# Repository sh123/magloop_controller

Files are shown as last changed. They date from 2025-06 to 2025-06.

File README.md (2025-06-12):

# Magnetic loop antenna capacitor controller
Magnetic loop antenna capacitor controller based on 
 - OpenSCAD project to generate custom sliding variable high voltage capacitors with two predefined configurations
 - Arduino Nano
 - L298N stepper driver
 - EM-290 stepper from Epson printer
 - HC-06 bluetooth serial controller for remote control using Bluetooth console application from the phone or PC
 - Generated high voltage 3d printed slide capacitor printed with PETG plastic (up to ~15kV and 130pF)
   - Plate sizes are ~70x55 mm
   - Capacitor dimensions are 60x70x80 mm
   - Plate spacing 5 mm
   - 14 plates
   - Worm gear is M4
   - Can handle 100W CW without arcing (tested with 0.9m loop) and continous 50W operation in FT8
   - Capacitance range ~5-130 pF
   - Can tune ~9-29 MHz with 0.9m loop
 - Second test generated medium voltage 3d printed slide capacitor up to ~6 kV and higher 400pF capacitance

# Serial commands
On successful command execution "ok" is returned when operation was successfully completed or "err" if command was unsuccessful. Next commands are supported:
 - Movements
   - *p*: park to initial 0 position, automatically performed when powered on
   - *u*, *uu*, *uuu*: go/tune up to higher frequency (5/50/500kHz steps)
   - *d*, *dd*, *ddd*: go/tune down to lower frequency (5/50/500kHz steps)
   - *freqkhz*, frequency in kHz where to move capacitor, should be used after calibration procedure completion
 - Calibration
   - *t*: print calibration table
   - *c[freqkhz]*: store current minimum swr position into given calibration frequency cell
   - *s*: save calibration table

# Configuration parameters (capctrl.h)
 - *ConfigSpeed*: stepper speed, default is 64
 - *ConfigStep(5|50|500)kHz*: number of steps for tune up/down commands for 5/50/500kHz steps
 - *ConfigMaxPos*: end position of capacitor, maximum number of steps, default is 5200
 - *ConfigCalPoints*: number of calibration points, default is 23
 - *ConfigCalAddr*: EEPROM start address where calibration data is stored, default is 0x0
 - *ConfigStepCompensate*: number of steps for reverse compensation when changing direction

# Photos

- Large capacitor 15kV/130pF

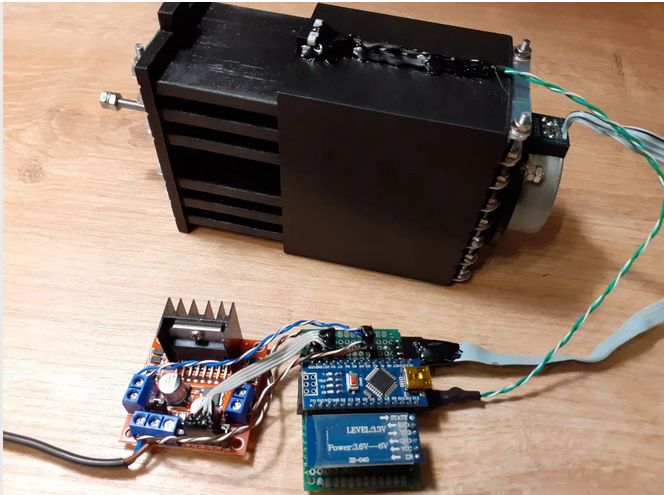
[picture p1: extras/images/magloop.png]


-  Medium size capacitor with lower maximum voltage, but larger capacitance 6kV/400pF

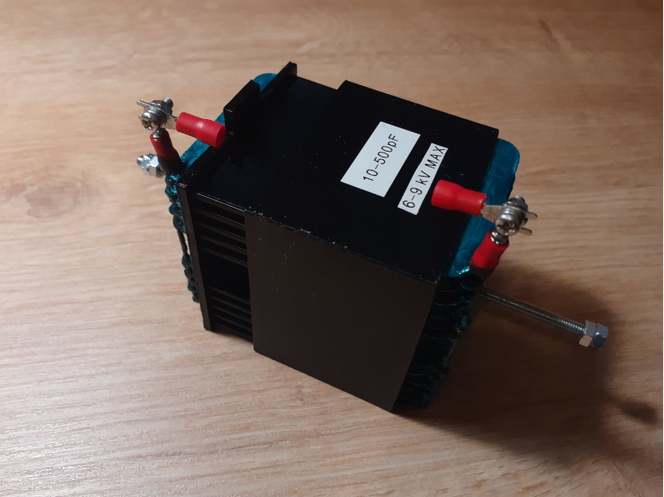
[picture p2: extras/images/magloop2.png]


- Test magnetic loop antenna, 1m loop diameter, 40mm tube diameter, fed using inductive coupling from smaller loop and 1:1 balun

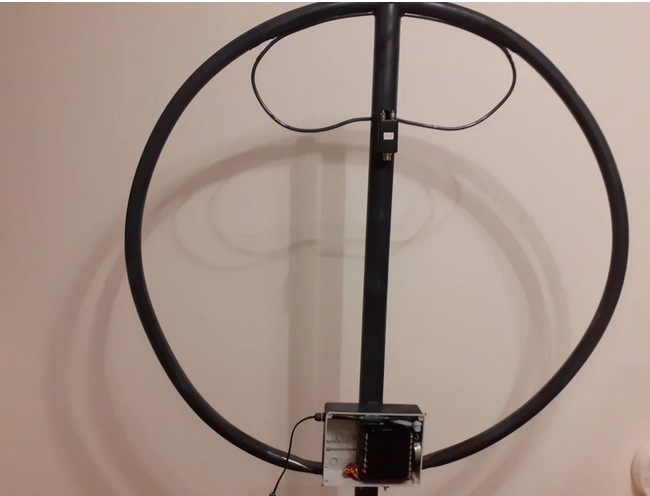
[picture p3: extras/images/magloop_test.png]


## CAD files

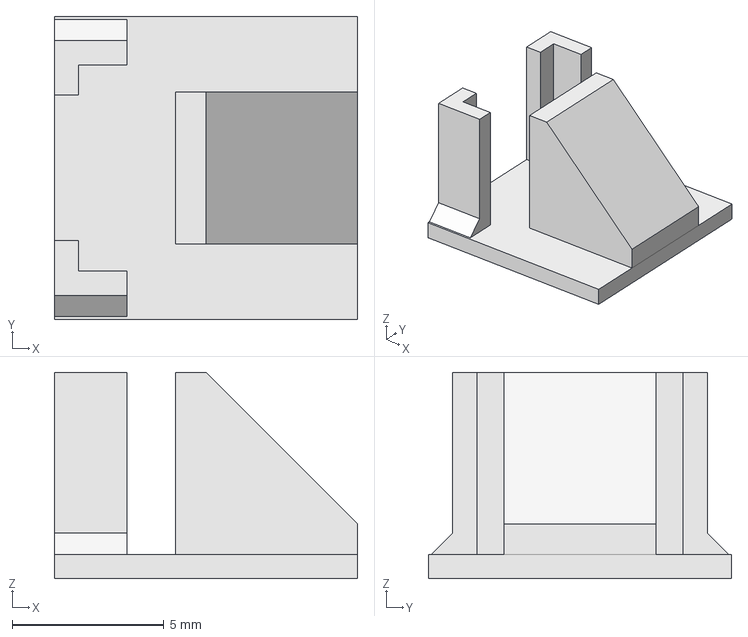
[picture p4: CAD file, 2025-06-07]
extras/cad/btn_holder.FCStd
10.0 x 10.0 x 6.80 mm

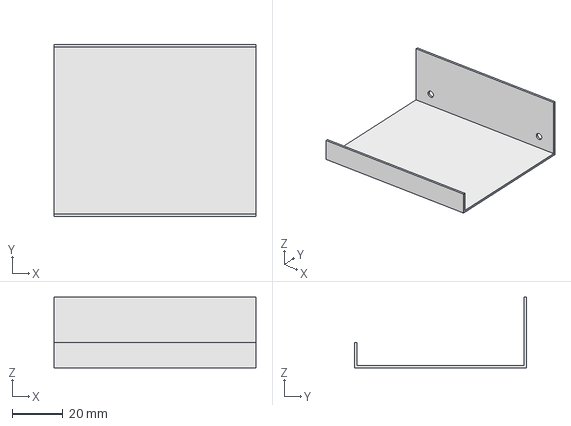
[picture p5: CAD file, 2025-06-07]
extras/cad/electronics_holder.FCStd
80.0 x 68.0 x 28.0 mm

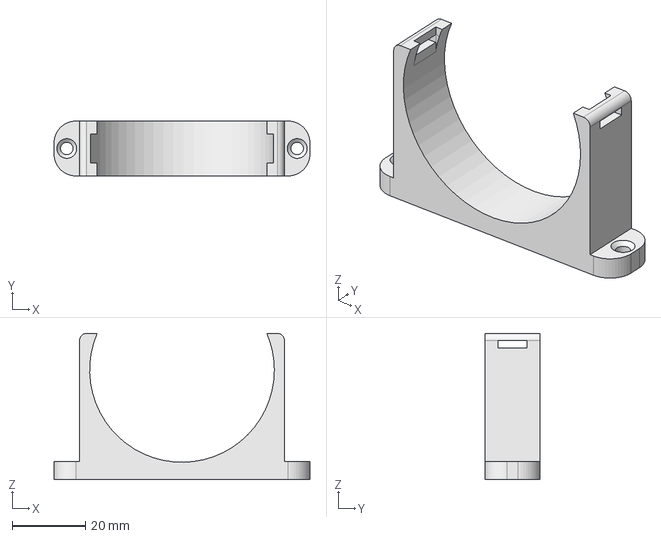
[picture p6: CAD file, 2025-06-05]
extras/cad/box_holder.FCStd
70.0 x 15.0 x 40.0 mm

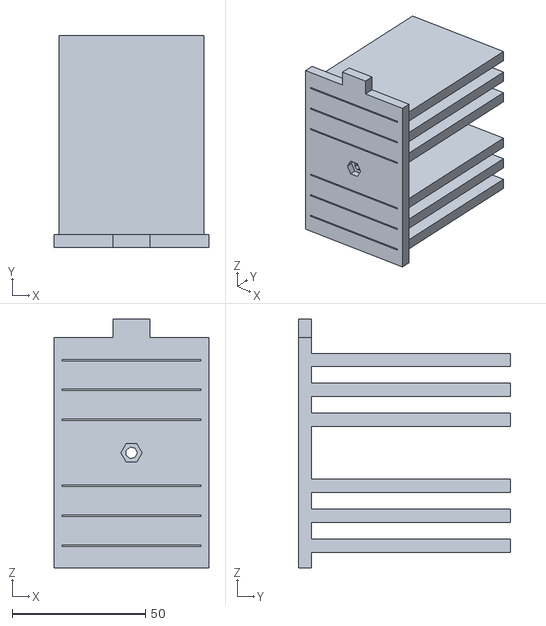
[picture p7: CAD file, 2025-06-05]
extras/cad/15kv_130pf_rotor.stl
58.0 x 79.7 x 93.4

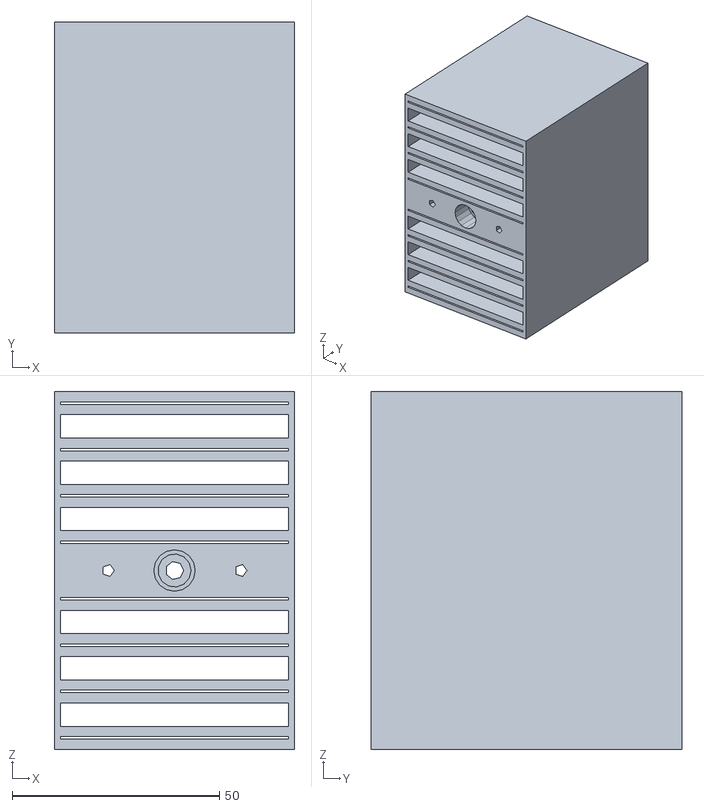
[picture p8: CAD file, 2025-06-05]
extras/cad/15kv_130pf_stator.stl
58.0 x 75.0 x 86.4

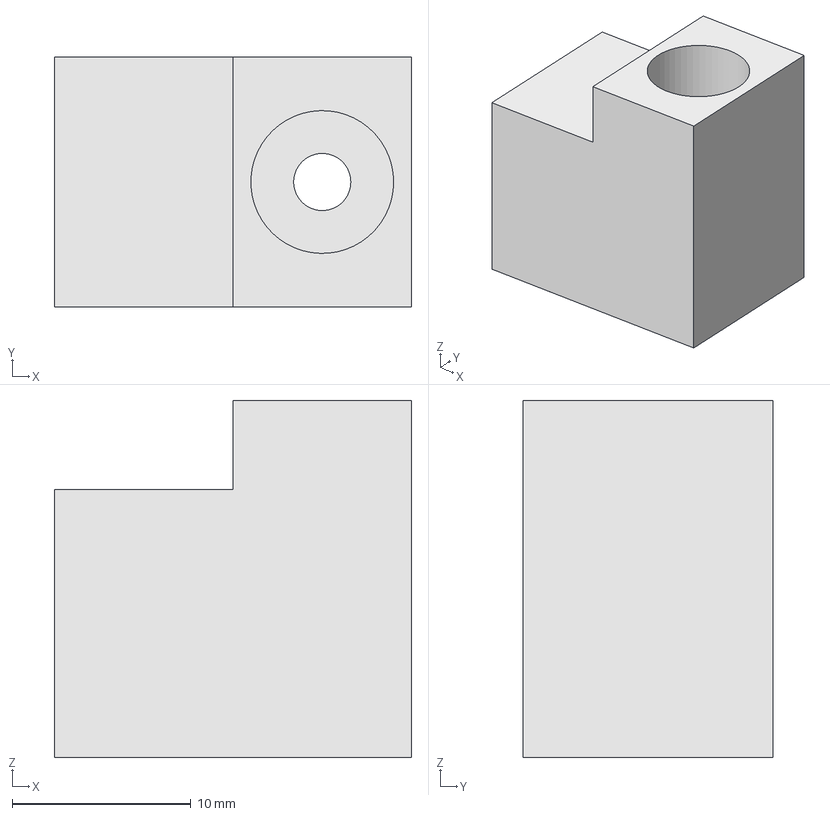
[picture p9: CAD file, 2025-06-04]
extras/cad/cap_stands_15mm.FCStd
20.0 x 14.0 x 20.0 mm

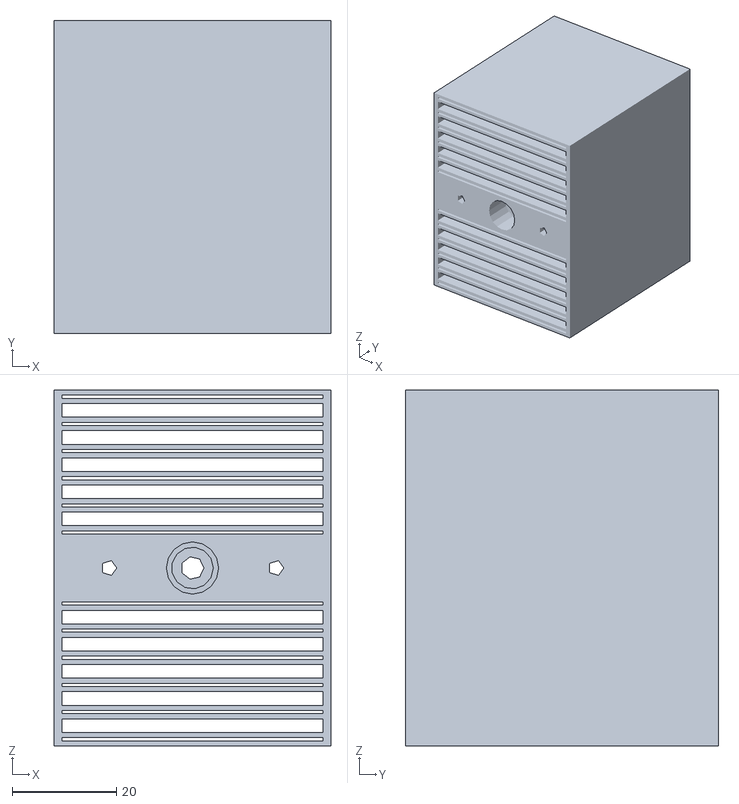
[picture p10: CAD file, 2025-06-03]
extras/cad/6kv_400pf_stator.stl
53.0 x 60.0 x 68.2

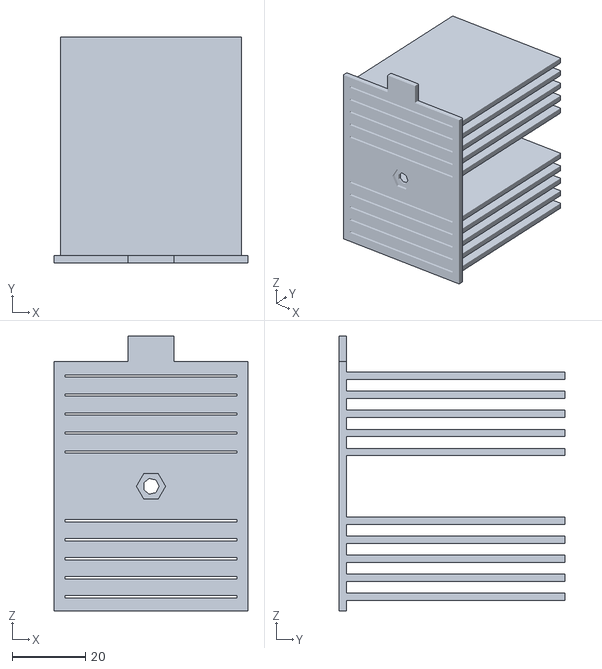
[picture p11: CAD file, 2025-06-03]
extras/cad/6kv_400pf_rotor.stl
53.0 x 61.7 x 75.2

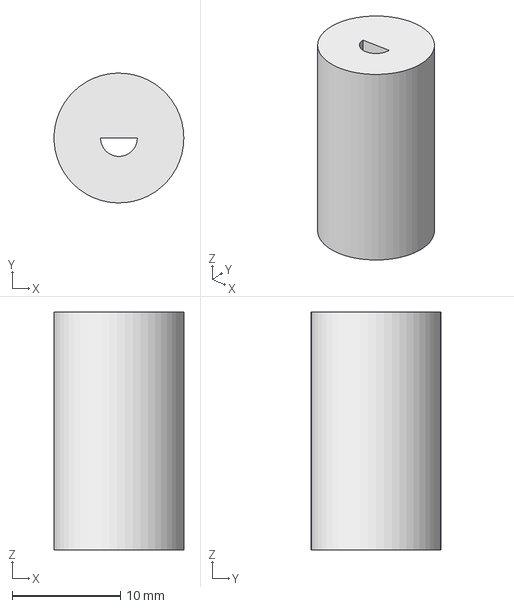
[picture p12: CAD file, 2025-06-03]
extras/cad/motor_em290_shaft.FCStd
12.0 x 12.0 x 22.0 mm

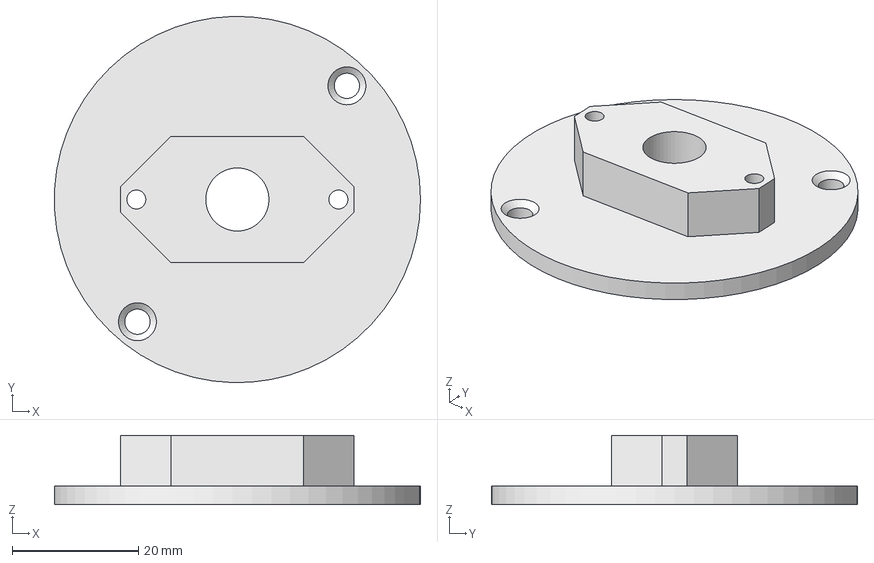
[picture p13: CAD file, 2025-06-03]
extras/cad/motor_em290_holder_small.FCStd
58.0 x 58.0 x 11.0 mm

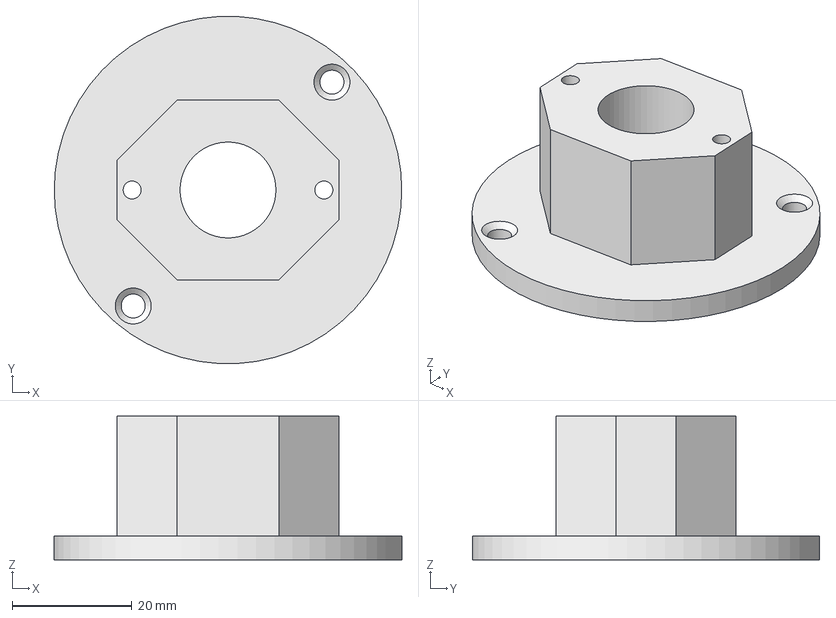
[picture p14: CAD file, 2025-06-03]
extras/cad/motor_em290_holder_medium.FCStd
58.0 x 57.9 x 24.0 mm

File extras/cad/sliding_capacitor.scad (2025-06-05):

/* [Main Parameters] */

// count of all plates in capacitor
plate_count_ = 13;           // [3, 5, 7, 9, 11, 13, 15, 17, 19, 21, 23, 25]

// distance between rotor and stator capacitor plates in mm
plate_distance_ = 5;         // [1, 2, 3, 4, 5, 6, 7, 8]

// capacitor plate width
plate_width_ = 55;

// capacitor plate height
plate_depth_ = 75;

// capacitor plate hole height, use larger value to make some room
plate_height_ = 0.6;

// gap between rotor and stator, tune for smoother sliding by printing tiny capacitor first, use acetone bath!
sliding_gap_ = 0.3;

// capacitor element to generate
generate_element_ = "stator";       // [stator, rotor]

// generate both stator and rotor for demo purposes?
generate_both_demo_ = "yes";        // [yes, no]

// enable worm gear system?
enable_worm_gear_ = "yes";          // [yes, no]

// enable button pusher?
enable_rotor_button_pusher_ = "yes";    // [yes, no]

/* [Worm Gear Parameters] */

// how much space to provide for worm gear system
worm_gear_gap_ = 8;

// worm shaft radius, change if use other than M4 shaft
worm_shaft_radius_ = 2;     // [1, 1.5, 2, 2.5, 3, 3.5, 4]

// bearing outer radius
bearing_radius_ = 4;

// bearing size depth/height
bearing_depth_ = 3;

// hole for screws, use larger diameter so tool will fit
screw_hole_radius_ = 6;

// depth of hole for screw, change based on shaft, number of nuts
screw_hole_depth_ = 8;

// hole sizes for stepper holder screws
holder_screw_radius_ = 1.5;

// distance from the shaft to the the motor holding screws
holder_screw_center_distance_ = 16;

// height of rotor button pusher    
button_pusher_height_ = 7;

// hole depth for holding nut on the rotor, change based on shaft, M3/M4/etc
nut_cutout_depth_ = 3.2;

// holding nut radius on the rotor, change based on shaft, M3/M4/etc
nut_cutout_radius_ = 4;
    
/* [Advanced Parameters] */

// gap between plate edge and stator edge
plate_width_guard_ = 1.5;

// depth of rotor base plate
rotor_base_plate_depth_ = 5;

assert(plate_count_ % 2 == 1, "Plate count must be an odd number");

echo("maximum capacitance: ~", capacitor_value_pf(plate_width_, plate_depth_, plate_count_, plate_distance_), "pF");
echo("breakdown voltage for air: ", breakdown_voltage_kv(3, plate_distance_), "kV");
echo("breakdown voltage for PETG: ", breakdown_voltage_kv(4.5, plate_distance_), "kV");

if (enable_worm_gear_ == "yes")
{
    assert(plate_count_ % 4 == 1, "Wrong plate count, must be one of [5, 9, 13, 17, 21, 25]");
    capacitor_with_worm_gear(plate_count_, plate_distance_, plate_width_, 
        plate_depth_, plate_height_, sliding_gap_, generate_element_, 
        generate_both_demo_, worm_gear_gap_, enable_rotor_button_pusher_);
} else 
{
    capacitor_naked(plate_count_, plate_distance_, plate_width_, 
        plate_depth_, plate_height_, sliding_gap_, generate_element_, generate_both_demo_);
}

// calculate capacitor breakdown voltage
function breakdown_voltage_kv(breakdown_voltage_mm, plate_distance) = plate_distance * breakdown_voltage_mm;

// calculate ~20% infill PETG filament approximate capacitor value from dimensions in mm and plate count
function capacitor_value_pf(plate_width, plate_depth, plate_count, plate_distance) =
    let (dielectric_constant = 1.55, electrostatic_constant = 8.854e-12)
        (plate_count - 1) * dielectric_constant * electrostatic_constant * plate_width * plate_depth / plate_distance * 1e9;

// generate capacitor with worm gear
module capacitor_with_worm_gear(plate_count, plate_distance, plate_width, 
    plate_depth, plate_height, sliding_gap, generate_element, generate_both_demo, 
    worm_gear_gap, enable_rotor_button_pusher)
{
    if (generate_element == "stator" || generate_both_demo == "yes") 
    {
        translate([0, 75, 0])
            capacitor_stator_with_worm_gear(plate_count, plate_distance, 
                plate_width, plate_depth, plate_height, worm_gear_gap);
    }
    if (generate_element == "rotor" || generate_both_demo == "yes") 
    {
        color("green")
            capacitor_rotor_with_worm_gear(plate_count, plate_distance, 
                plate_width, plate_depth, plate_height, sliding_gap, worm_gear_gap, enable_rotor_button_pusher);
    }
}

// generate capacitor
module capacitor_naked(plate_count, plate_distance, plate_width, 
    plate_depth, plate_height, sliding_gap, generate_element, generate_both_demo)
{
    if (generate_element == "stator" || generate_both_demo == "yes") 
    {
        translate([0, 50, 0])
            capacitor_stator(plate_count, plate_distance, 
                plate_width, plate_depth, plate_height);
    }
    if (generate_element == "rotor" || generate_both_demo == "yes") 
    {
        color("green")
            capacitor_rotor(plate_count, plate_distance, 
                plate_width, plate_depth, plate_height, sliding_gap);
    }
}

// generate stator with worm gear support
module capacitor_stator_with_worm_gear(plate_count, plate_distance, 
    plate_width, plate_depth, plate_height, worm_gear_gap)
{
    plate_width_guard = plate_width_guard_;
    worm_shaft_radius = worm_shaft_radius_;
    bearing_radius = bearing_radius_;
    bearing_depth = bearing_depth_;
    screw_hole_radius = screw_hole_radius_;
    screw_hole_depth = screw_hole_depth_;
    holder_screw_radius = holder_screw_radius_;
    holder_screw_center_distance = holder_screw_center_distance_;
    
    holder_screw_depth = plate_depth;
    bearing_full_depth = bearing_depth + screw_hole_depth;
    half_plate_count = ceil(plate_count / 2.0);
    box_height = half_plate_count * (plate_distance + plate_height);
    box_height_center = box_height + worm_gear_gap / 2.0;
    box_width_center = plate_width / 2.0 + plate_width_guard;
    
    difference()
    {
        // stator body with holes
        union()
        {
            // two split capacitor stators
            translate([0, 0, 0])
                capacitor_stator(half_plate_count, plate_distance, plate_width, plate_depth, plate_height);
            translate([0, 0, box_height + worm_gear_gap])
                capacitor_stator(half_plate_count, plate_distance, plate_width, plate_depth, plate_height);
            
            // worm gear blade hole
            translate([0, 0, box_height])
                cube([plate_width + 2 * plate_width_guard, plate_depth, worm_gear_gap]);
        }
        
        // worm gear system
        translate([plate_width / 2.0 + plate_width_guard, 0, box_height_center])
            rotate([-90, 0, 0])
                union() 
                {
                    cylinder(plate_depth, r=worm_shaft_radius + 0.2);
                    cylinder(bearing_full_depth, r=bearing_radius);
                    cylinder(screw_hole_depth, r=bearing_radius + 1);
                }
        translate([box_width_center, plate_depth - bearing_full_depth, box_height_center])
            rotate([-90, 0, 0])
                cylinder(bearing_full_depth, r=bearing_radius);
        translate([box_width_center, plate_depth - screw_hole_depth, box_height_center])
            rotate([-90, 0, 0])
                cylinder(screw_hole_depth, r=screw_hole_radius);

        // holder holes
        translate([box_width_center + holder_screw_center_distance, plate_depth - holder_screw_depth, box_height_center])
            rotate([-90, 0, 0])
                cylinder(holder_screw_depth, r=holder_screw_radius);
        translate([box_width_center - holder_screw_center_distance, plate_depth - holder_screw_depth, box_height_center])
            rotate([-90, 0, 0])
                cylinder(holder_screw_depth, r=holder_screw_radius);
    }
}

// generate rotor with worm gear support
module capacitor_rotor_with_worm_gear(plate_count, plate_distance, 
    plate_width, plate_depth, plate_height, sliding_gap, 
    worm_gear_gap, enable_rotor_button_pusher)
{
    plate_width_guard = plate_width_guard_;
    worm_shaft_radius = worm_shaft_radius_;
    base_plate_width = rotor_base_plate_depth_;
    nut_cutout_depth = nut_cutout_depth_;
    nut_cutout_radius = nut_cutout_radius_;
    button_pusher_height = button_pusher_height_;

    half_plate_count = ceil(plate_count / 2.0);
    
    box_height = half_plate_count * (plate_distance + plate_height);
    box_height_center = box_height + worm_gear_gap / 2.0;
    box_width_center = plate_width / 2.0 + plate_width_guard;
    
    button_pusher_height_pos = 2 * box_height + worm_gear_gap;
    button_pusher_width = plate_width / 4.0;
    button_pusher_width_center = box_width_center - button_pusher_width / 2.0;
    button_pusher_depth = base_plate_width;
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

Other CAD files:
extras/cad/box_holder.stl
extras/cad/btn_holder.stl
extras/cad/cap_stands_15mm.stl
extras/cad/electronics_holder.stl
extras/cad/motor_em290_holder_medium.stl
extras/cad/motor_em290_holder_small.stl
extras/cad/motor_em290_shaft.stl

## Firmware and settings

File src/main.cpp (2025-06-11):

#include <SoftwareSerial.h>
#include <Stepper.h>
#include "capctrl.h"

#define STEPS     200
#define BTN_STOP  11

String currentCommand;

SoftwareSerial btCtrl(9, 10); // our RX, TX, hc06 TX, RX
CapCtrl capCtrl(STEPS, A2, A3, A4, A5, BTN_STOP);

void println(const String &s) 
{
  Serial.println(s);
  btCtrl.println(s);  
}

void setup() 
{
  Serial.begin(115200);
  btCtrl.begin(9600);
  
  println(F("started"));
  capCtrl.park();
  println(F("parked"));
}

bool readChar(char &c)
{
  bool found = true;
  
  if (Serial.available()) 
    c = Serial.read(); 
  else if (btCtrl.available())
    c = btCtrl.read();
  else
    found = false;
    
  return found;
}

String readLine() 
{
  String result;

  while (1) 
  {
    char newChar;
      
    if (readChar(newChar)) 
    {
      if (newChar == '\n') 
        return result;
      else if (newChar == '\r') {}
      else 
        result += newChar;  
    }
    delay(100);
  }
}

void runCommand(const String &cmd) 
{
  // help
  if (cmd == "h") 
  {
    println(F("(u/d/uu/dd/uuu/ddd/p)/(c<freq>/t/s)/<freq>"));
  }
  // down
  else if (cmd == "d") 
  {
    capCtrl.down5kHz();
  }
  else if (cmd == "dd") 
  {
    capCtrl.down50kHz();
  }
  else if (cmd == "ddd") 
  {
    capCtrl.down500kHz();
  }
  // up
  else if (cmd == "u") 
  {
    capCtrl.up5kHz();
  }
  else if (cmd == "uu") 
  {
    capCtrl.up50kHz();
  }
  else if (cmd == "uuu") 
  {
    capCtrl.up500kHz();
  }
  // park
  else if (cmd == "p") 
  {
    capCtrl.park();
  }
  // calibrate
  else if (cmd[0] == 'c') 
  {
    String freq = cmd.substring(1);
    if (!capCtrl.calStore(freq.toInt())) 
    {
      println(F("unknown freq"));
      return;
    }
    capCtrl.calSave();
  }
  // print calibration table
  else if (cmd == "t") 
  {
    capCtrl.calPrint(println);
  }
  // save calibration table
  else if (cmd == "s") 
  {
    capCtrl.calSave();
  }
  // go to frequency
  else 
  {
    long freqKhz = cmd.toInt();
    
    if (!capCtrl.setFreq(freqKhz)) 
    {
      println(F("wrong freq"));
      return;
    }
  }
  println("ok, " + String(capCtrl.getPos()));
}

void loop()
{ 
  char cmd;
  
  if (readChar(cmd)) 
  {
    if (cmd == '\n')
    {
      runCommand(currentCommand);
      currentCommand = String();
    }
    else if (cmd == '\r') {}
    else 
    {
      currentCommand += cmd;  
    }
  }
}

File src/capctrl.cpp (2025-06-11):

#include "capctrl.h"

struct CapCtrl::CalPoint CapCtrl::calPoints_[] = 
{
  // 30m
  { 1620, 10100 },
  { 1670, 10120 },
  { 1720, 10140 },
  // 20m
  { 2990, 14000 },
  { 3070, 14170 },
  { 3150, 14350 },
  // 17m
  { 3640, 18068 },
  { 3680, 18110 },
  { 3700, 18168 },
  // 15m
  { 3860, 21000 },
  { 3880, 21225 },
  { 3900, 21450 },
  // 12m
  { 4360, 24890 },
  { 4360, 24940 },
  { 4360, 24990 },
  // 11m
  { 4640, 27000 },
  { 4700, 27100 },
  { 4800, 27300 },
  { 4900, 27500 },
  { 4980, 27600 },
  // 10m
  { 5080, 28000 },
  { 5100, 28200 },
  { 5200, 28500 },
};

CapCtrl::CapCtrl(int steps, int pin1, int pin2, int pin3, int pin4, int pinBtn)
  : prevDir_(ConfigDirNone)
  , pos_(0)
  , stepper_(steps, pin1, pin2, pin3, pin4)
  , pin1_(pin1)
  , pin2_(pin2)
  , pin3_(pin3)
  , pin4_(pin4)
  , pinBtn_(pinBtn)
{
  // set default speed and button mode
  stepper_.setSpeed(ConfigSpeed);
  pinMode(pinBtn, INPUT_PULLUP);
  
  // store default table on first time run
  int probe = 0;
  EEPROM.get(ConfigCalAddr, probe);
  if (probe == -1)
    calSave();
  else
    calLoad();
}

CapCtrl::~CapCtrl() 
{
}

bool CapCtrl::setPos(int newPos)
{
  if (newPos < 0 || newPos > ConfigMaxPos)
    return false;

  stepper_.setSpeed(ConfigSpeed);
  int dir = newPos > pos_ ? ConfigDirUp : ConfigDirDn;
  
  while (pos_ != newPos) 
  {
    pos_ += dir;
    stepper_.step(-dir);
  }
  compensate(dir);
  releaseMotor();
  return true;
}

bool CapCtrl::setFreq(long freqKhz)
{
  if (freqKhz == 0)
    return false;

  for (int i = 0; i < ConfigCalPoints - 1; i++) 
  {
    long freqA = calPoints_[i].freqKhz;
    long freqB = calPoints_[i + 1].freqKhz;

    if (freqKhz >= freqA && freqKhz < freqB) 
    {
        long posA = calPoints_[i].pos;
        long posB = calPoints_[i + 1].pos;

        long pos = (posA * (freqB - freqKhz) + posB * (freqKhz - freqA)) / (freqB - freqA);

        return setPos(pos);
    }
  }
  return false;
}

void CapCtrl::park()
{
  stepper_.setSpeed(ConfigSpeed);

  while (digitalRead(pinBtn_) == ConfigBtnDisabled)
    stepper_.step(1);

  releaseMotor();
  
  pos_ = 0;
}

void CapCtrl::compensate(int dir) 
{   
  if (prevDir_ != ConfigDirNone && prevDir_ != dir) 
  {
    stepper_.step(-dir * ConfigStepCompensate);
  }
  prevDir_ = dir;
}

void CapCtrl::up5kHz()
{
  up(ConfigStep5kHz, ConfigSpeed);
}

void CapCtrl::down5kHz()
{
  down(ConfigStep5kHz, ConfigSpeed);
}

void CapCtrl::up50kHz()
{
  up(ConfigStep50kHz, ConfigSpeed);
}

void CapCtrl::down50kHz()
{
  down(ConfigStep50kHz, ConfigSpeed);
}

void CapCtrl::up500kHz()
{
  up(ConfigStep500kHz, ConfigSpeed);
}

void CapCtrl::down500kHz()
{
  down(ConfigStep500kHz, ConfigSpeed);
}

void CapCtrl::up(int step, int speed)
{
  if (pos_ + step <= ConfigMaxPos)
  {
    stepper_.setSpeed(speed);
    stepper_.step(-step);
    compensate(ConfigDirUp);
    stepper_.setSpeed(speed);
    pos_ += step;
    releaseMotor();
  }
}

void CapCtrl::down(int step, int speed)
{
  if (digitalRead(pinBtn_) == ConfigBtnDisabled && pos_ - step >= 0) 
  {
    stepper_.setSpeed(speed);
    stepper_.step(step);
    compensate(ConfigDirDn);
    stepper_.setSpeed(speed);
    pos_ -= step;
    releaseMotor();
  }
}

void CapCtrl::releaseMotor()
{
  digitalWrite(pin1_, LOW);  
  digitalWrite(pin2_, LOW);
  digitalWrite(pin3_, LOW);
  digitalWrite(pin4_, LOW);
}

void CapCtrl::calSave() 
{
  for (int i = 0; i < ConfigCalPoints; i++)
    EEPROM.put(ConfigCalAddr + i * sizeof(CalPoint), calPoints_[i]);
}

void CapCtrl::calLoad() 
{
  for (int i = 0; i < ConfigCalPoints; i++)
    EEPROM.get(ConfigCalAddr + i * sizeof(CalPoint), calPoints_[i]);
}

bool CapCtrl::calMove(int index)
{ 
  if (index >= 0 && index < ConfigCalPoints)
    return setPos((long)index * (long)ConfigMaxPos / ConfigCalPoints);
    
  return false;
}

bool CapCtrl::calStore(int freqKhz)
{
  for (int i = 0; i < ConfigCalPoints; i++)
  {
    if (calPoints_[i].freqKhz == freqKhz) 
    {
      calPoints_[i].pos = pos_;
      return true;
    }
  }
  return false;
}

void CapCtrl::calPrint(t_print print) 
{
  for (int i = 0; i < ConfigCalPoints; i++)
  {
    print(String(calPoints_[i].pos) + ":" + String(calPoints_[i].freqKhz));
  }
}

bool CapCtrl::calStore(int index, int freqKhz)
{
  if (index >= 0 && index < ConfigMaxPos)
  {
    calPoints_[index].pos = (long)index * (long)ConfigMaxPos / ConfigCalPoints;
    calPoints_[index].freqKhz = freqKhz;
    
    return true;
  }
  return false;
}

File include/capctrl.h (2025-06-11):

#ifndef CAPCTRL_H
#define CAPCTRL_H

#include <Arduino.h>
#include <Stepper.h>
#include <EEPROM.h>
#include <SoftwareSerial.h>

typedef void (*t_print)(const String &s);

class CapCtrl 
{
  struct CalPoint 
  {
    int pos;
    int freqKhz; 
  } CalPoint_t;
  
public:
  CapCtrl(int steps, int pin1, int pin2, int pin3, int pin4, int pinBtn);
  ~CapCtrl();
  
  bool setFreq(long freqKhz);
  int getPos() const { return pos_; }

  bool calStore(int freqKhz);
  void calSave();
  void calPrint(t_print print);
  
  void park();
  
  void up5kHz();
  void down5kHz();
  void up50kHz();
  void down50kHz();
  void up500kHz();
  void down500kHz();

private:
  bool setPos(int newPos);
  void releaseMotor();
  void compensate(int dir);

  void up(int step, int speed);
  void down(int step, int speed);
 
  void calLoad();
  bool calMove(int index);
  bool calStore(int index, int freqKhz);

private:
  const int ConfigSpeed = 64;
  const int ConfigStep5kHz = 5; 
  const int ConfigStep50kHz = 17;
  const int ConfigStep500kHz = 90;
  const int ConfigStepCompensate = 14;
  const int ConfigMaxPos = 5200;
  const int ConfigBtnDisabled = 1;

  const int ConfigCalPoints = 23;
  const int ConfigCalAddr = 0x0;

  const int ConfigDirUp = 1;
  const int ConfigDirNone = 0;
  const int ConfigDirDn = -1;

private:
  int prevDir_;
  int pos_;
  Stepper stepper_;
  int pin1_, pin2_, pin3_, pin4_, pinBtn_;

  static CalPoint calPoints_[];
};

#endif // CAPCTRL_H

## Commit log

2020-02-09 Add methods for storing and reading calibration data from EEPROM
2020-02-09 Implement methods for moving to specific calibration index and storing its frequency
2020-02-09 Add moving to position based on linear interpolation over calibrated values
2020-02-09 Implement calibratio and navigation to given frquency
2020-02-10 Added images and models
    [cap_slide_base.FCStd, cap_slide_base.stl, cap_slide_base_large.FCStd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]
2020-02-24 Fix bug with calibration
    [magloop_controller.ino]
2020-02-24 Fix wrong boundary condition
    [capctrl.cpp]
2020-02-24 Increase number of calibration points
2020-09-12 Added OpenSCAD capacitor model
    [sliding_capacitor.scad]
2020-09-12 Remove stl models
    [cap_slide_base.stl, cap_slide_base_large.stl, cap_slide_mover.stl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]
2020-09-19 Change the way calibration is done
2023-03-20 Moved to platformio
    [cap_slide_base.FCStd, cap_slide_base_large.FCStd, cap_slide_mover.FCStd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]
2023-03-20 Minor fixes
    [sliding_capacitor.scad]
2023-03-22 Update default settings
    [sliding_capacitor.scad]
2023-03-25 Added manual knob
    [knob.FCStd]
2025-06-03 Remove unused models
    [cap_slide_base.FCStd, cap_slide_base_large.FCStd, cap_slide_mover.FCStd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]
2025-06-03 Added new models
    [15kv_rotor.stl, 15kv_stator.stl, motor_holder_medium.FCStd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]
2025-06-03 Added another generated model
    [6kv_400pf_rotor.stl, 6kv_400pf_stator.stl]
2025-06-04 Added cap stands
    [cap_stands_15mm.FCStd, cap_stands_15mm.stl]
2025-06-05 Update scad model
    [sliding_capacitor.scad]
2025-06-05 Update models
    [15kv_130pf_rotor.stl, 15kv_130pf_stator.stl]
2025-06-05 Added box holder models
    [box_holder.FCStd, box_holder.stl]
